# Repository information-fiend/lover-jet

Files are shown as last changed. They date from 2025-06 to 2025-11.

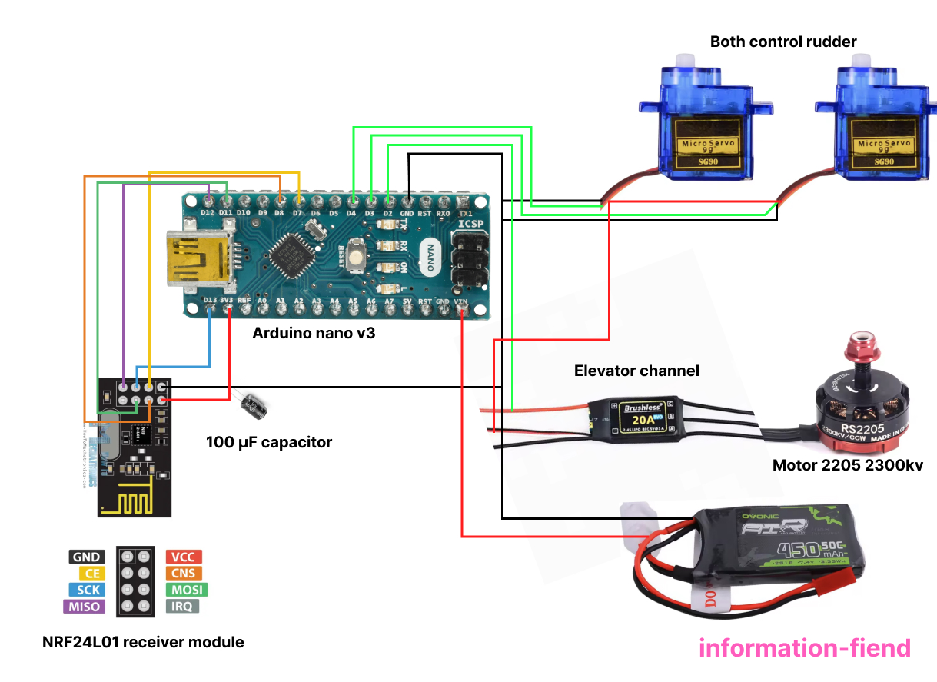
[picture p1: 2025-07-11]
Wiring diagrams/wiring diagram 3.jpg

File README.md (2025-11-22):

<h2 align="center">
 
 Lover Jet: RC F-22 Raptor
</h2>
&nbsp;

> A lover, not a fighter. :warning: Not to mock or make light of warfare

A 4-channel RC system consisting of a Arduino Nano-based transmitter and a cardboard F-22 Raptor jet powered by brushless propulsion. It uses NRF24L01+ transceivers for communication. Made this as an introduction to aerospace systems, more to come :)

### 📷 Pictures




Screenshot 2025-07-10 at 10 28 30 PM
(Cardboard jet hasnt been cut out yet)

### BOM
|Qty| Device|	Link	|Cost	|
|---|-----|---|---|
1|Cardboard 60x85cm|Me|N/A
1|Motor 2205 2300kv|[Link](https://www.aliexpress.us/item/3256806652883904.html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)|$0.99
1|Propeller 5045|[Link](https://www.aliexpress.us/item/3256806957215026.html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)|$5.53
1|ESC 20A FMS|[Link](https://www.aliexpress.us/item/3256807612408276.html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)|$0.99
2|Servo 9g|[Link](https://www.aliexpress.us/item/3256805670877496.html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)|$0.99
1|NRF24L01 receiver module|[Link](https://www.aliexpress.us/item/3256807924390952.html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)|$3.64
2|7.4v 450mah li-po battery|[Link](https://www.aliexpress.us/item/3256807759429745.html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)|$11.58
2|Arduino nano v3.0|[Link](https://www.amazon.com/LAFVIN-Board-ATmega328P-Micro-Controller-Arduino/dp/B07G99NNXL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)|$15.99
2|KY-023 joystick|[Link](https://www.aliexpress.us/item/3256807375670744.html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)|$1.77
1|NRF24L01 + PA|[Link](https://www.aliexpress.us/item/3256805495903750.html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)|$2.30
1|Single Pole Single Throw (SPST) Switch|[Link](https://www.aliexpress.us/item/3256808934087455.html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)|$1.48
1|EC11 rotary encoder|[Link](https://www.aliexpress.us/item/3256807457768762.html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)|$2.15
1|Voltage regulator 7805|[Link](https://www.aliexpress.us/item/3256807345258850.html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)|$1.95
2|100 µF capacitor|[Link](https://www.aliexpress.us/item/3256805372329013.html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)|$1.99
2|10 µF capacitor|[Link](https://www.aliexpress.us/item/3256805372329013.html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)|$1.99
1|AMS1117-3.3v|[Link](https://www.aliexpress.us/item/3256808067206574.html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)|$1.99
1|pcb| |$20.00
| | | |= $77.32

 <p align="center">
  
</p>

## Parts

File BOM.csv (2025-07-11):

Qty | Device | Link | Cost
1 | Cardboard 60x85cm | Me | N/A
1 | Motor 2205 2300kv | https://www.aliexpress.us/item/3256806652883904.html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 | $0.99
1 | Propeller 5045 | https://www.aliexpress.us/item/3256806957215026.html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 | $5.53
1 | ESC 20A FMS | https://www.aliexpress.us/item/3256807612408276.html | $0.99
2 | Servo 9g | https://www.aliexpress.us/item/3256805670877496.html | $0.99
1 | NRF24L01 receiver module | https://www.aliexpress.us/item/3256807924390952.html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 | $3.64
2 | 7.4v 450mah li-po battery | https://www.aliexpress.us/item/3256807759429745.html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 | $11.58
2 | Arduino nano v3.0 | https://www.amazon.com/LAFVIN-Board-ATmega328P-Micro-Controller-Arduino/dp/B07G99NNXL?xpid=BLck2ap9v-6h8 | $15.99
2 | KY-023 joystick | https://www.aliexpress.us/item/3256807375670744.html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 | $1.77
1 | NRF24L01 + PA | https://www.aliexpress.us/item/3256805495903750.html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 | $2.30
1 | Single Pole Single Throw (SPST) Switch | https://www.aliexpress.us/item/3256808934087455.html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 | $1.48
1 | EC11 rotary encoder | https://www.aliexpress.us/item/3256807457768762.html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 | $2.15
1 | Voltage regulator 7805 | https://www.aliexpress.us/item/3256807345258850.html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 | $1.95
2 | 100 µF capacitor | https://www.aliexpress.us/item/3256805372329013.html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 | $1.99
2 | 10 µF capacitor | https://www.aliexpress.us/item/3256805372329013.html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 | $1.99
1 | AMS1117-3.3v | https://www.aliexpress.us/item/3256808067206574.html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 | $1.99
1 | Perfboard | https://www.aliexpress.us/item/3256806952917702.html?scm_id=1007.40196.439370.0&scm-url=1007.40196.439370.0 | $1.99
1 | pcb |  | $20.00
 |  |  | $77.32

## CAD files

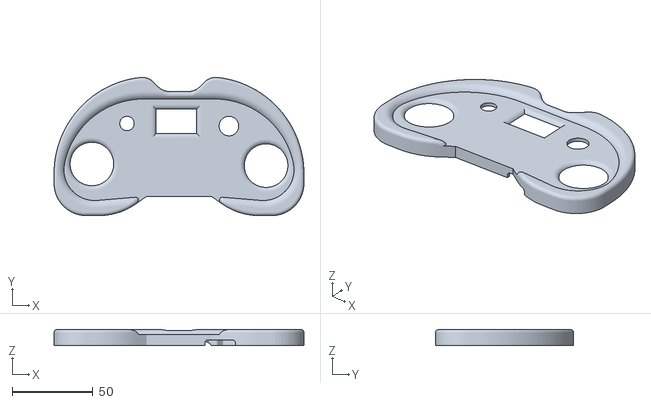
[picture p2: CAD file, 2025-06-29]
Production/front.stl
155.0 x 85.7 x 10.0

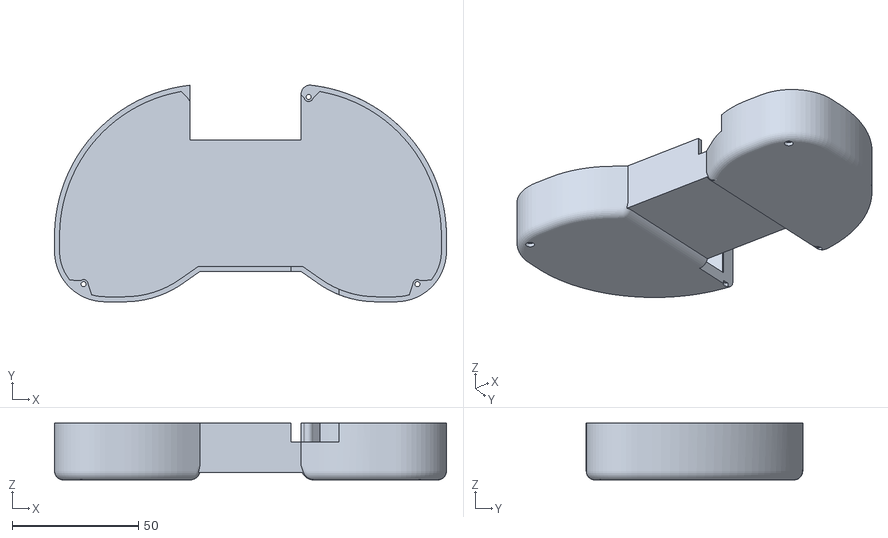
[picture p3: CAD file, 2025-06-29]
Production/back.stl
155.0 x 85.7 x 22.5

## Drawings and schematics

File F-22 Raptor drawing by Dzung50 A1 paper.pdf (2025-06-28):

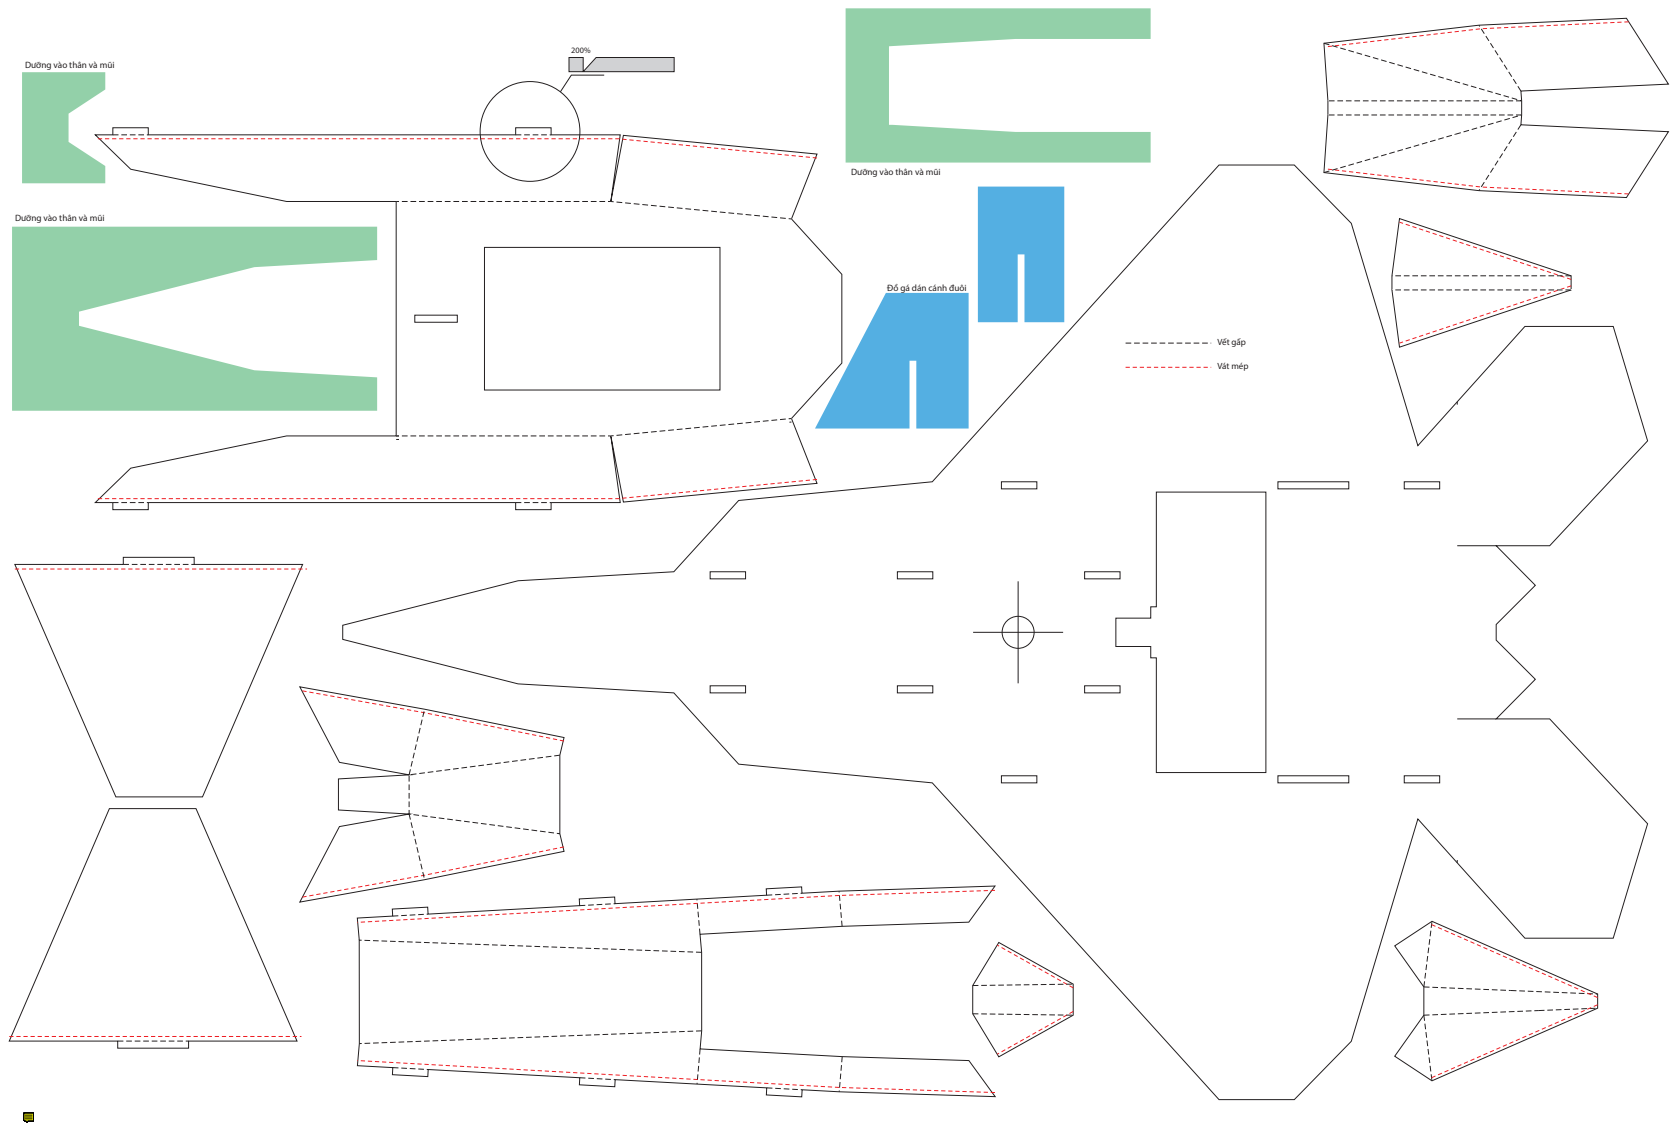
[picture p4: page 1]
Vết gấp; Vát mép

Dưỡng vào thân và mũi

Đồ gá dán cánh đuôi

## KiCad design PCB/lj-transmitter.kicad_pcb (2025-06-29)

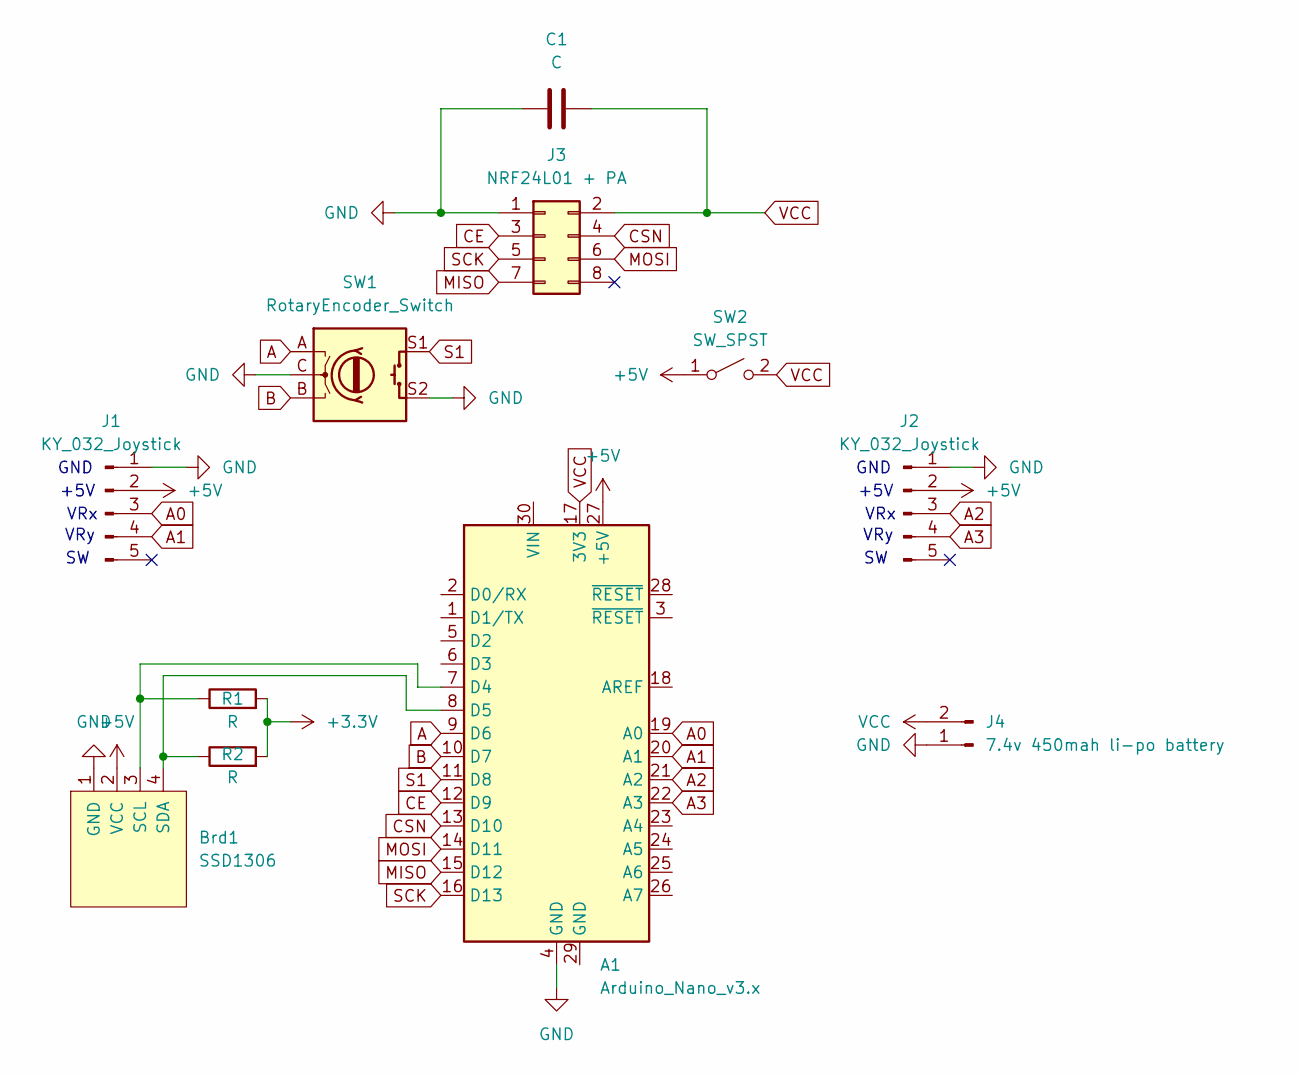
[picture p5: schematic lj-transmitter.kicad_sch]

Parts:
A1: Arduino_Nano_v3.x; Arduino_Nano
Brd1: SSD1306; 128x64OLED
C1: C; CP_Radial_D8.0mm_P5.00mm
J1, J2: KY_032_Joystick; PinHeader_1x05_P1.00mm_Vertical
J3: NRF24L01 + PA; nRF24L01_Breakout
J4: 7.4v 450mah li-po battery; BatteryHolder_Keystone_3034_1x20mm
R1, R2: R; R_Axial_DIN0207_L6.3mm_D2.5mm_P7.62mm_Horizontal
SW1: RotaryEncoder_Switch; RotaryEncoder_Alps_EC11E-Switch_Vertical_H20mm_CircularMoun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
SW2: SW_SPST; SW_CW_GPTS203211B

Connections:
+3.3V: R1.2, R2.2
+5V: A1.27 (+5V), Brd1.2 (VCC), J1.2, J2.2, SW2.1 (A)
A: A1.9 (D6), SW1.A
A0: A1.19 (A0), J1.3
A1: A1.20 (A1), J1.4
A2: A1.21 (A2), J2.3
A3: A1.22 (A3), J2.4
B: A1.10 (D7), SW1.B
CE: A1.12 (D9), J3.3
CSN: A1.13 (D10), J3.4
GND: A1.4 (GND), Brd1.1 (GND), C1.1, J1.1, J2.1, J3.1, J4.1, SW1.C, SW1.S2
MISO: A1.15 (D12), J3.7
MOSI: A1.14 (D11), J3.6
unnamed: A1.7 (D4), Brd1.3 (SCL), R1.1
unnamed: A1.8 (D5), Brd1.4 (SDA), R2.1
S1: A1.11 (D8), SW1.S1
SCK: A1.16 (D13), J3.5
VCC: A1.17 (3V3), C1.2, J3.2, J4.2, SW2.2 (B)

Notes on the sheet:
VRy
+5V
GND
VRx

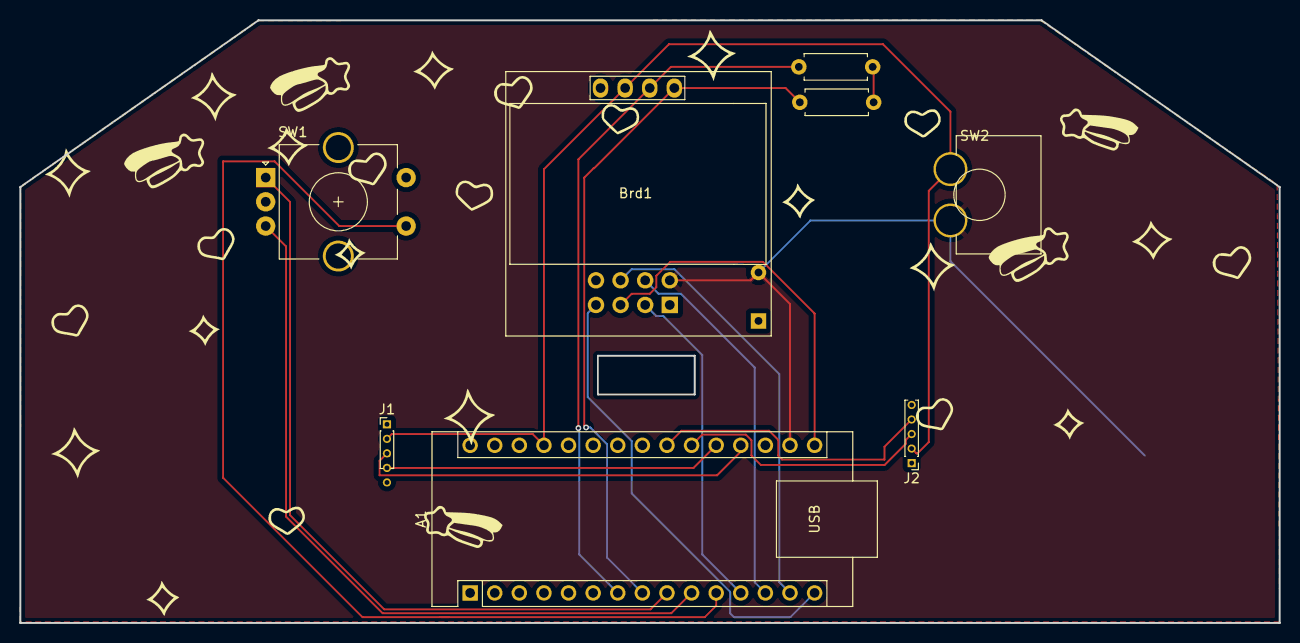
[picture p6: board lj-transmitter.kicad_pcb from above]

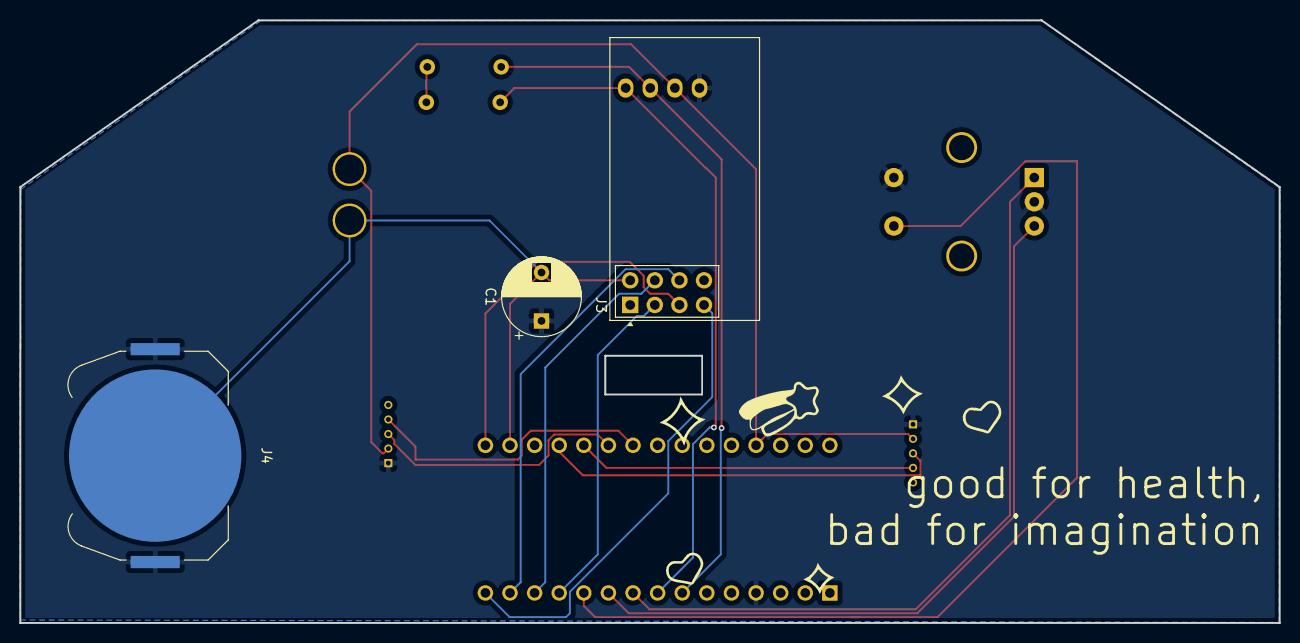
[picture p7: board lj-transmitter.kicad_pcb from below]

Board: 2 copper layers, 130.0 x 62.2 mm, 11 parts (3 on the bottom side), 18 nets.

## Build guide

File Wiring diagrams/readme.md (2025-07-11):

this is the wiring for the plane itself.
#1 is one i got from YT, shows the wires better. 
#2 i made on figma. its all the parts im using exactly.

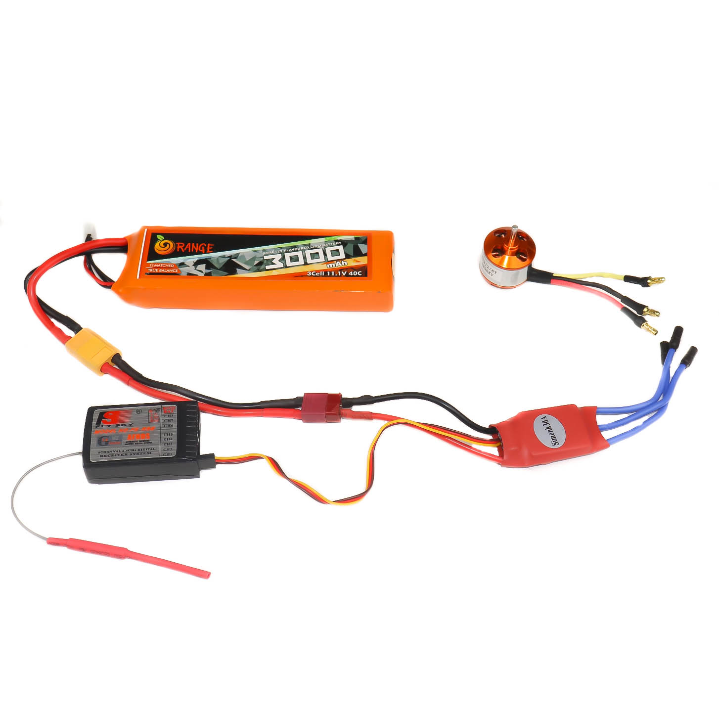
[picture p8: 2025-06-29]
Wiring diagrams/wiring diagram 1.jpg

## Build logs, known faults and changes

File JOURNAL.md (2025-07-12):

---
title: "lover-jet"
author: "info-fiend"
description: "F-22 Raptor with transmitter"
created_at: "2025-06-27"
---
### :revolving_hearts: Total Time Spent: 34hrs
June 27, 2025
---
*LOG #001:*
SPEED RUNNNNNN! rabbitboard took way too long (exactly a month). wanna get this done by the end of June cause July is busyyy. so first i started with a document and wrote everything about the project. at first it was just going to be the RC plane, but transmitters are $$$ so im gunna make that too. then i watched a bunch of vids on i. indidentally, it seems the transmitter is going to be more work than the plane 0_o. i was just going to stick a nano and antenna on a perfboard but we care about aesthetics around here. i started with making the wiring diagrams for both the transmitter and plane. started on wowki bcos i was too lazy to make a tinkercad account. am going to switch there probably. so a problem im running into is that i dont know a lick of C++, so making the firmware for the tranmitter makes me cry. <br/><br/>PLANE MATERIALS: 
* cardboard
* motor 2205 2300kv
* propeller 5045
* esc 20A FMS (eletric speed controller thing)
* 2x servos 9g
* LiPo battery
* mc6re reviever 
<br/><br/>TRANSMITTER MATS: 
* battery
* 2x joy sticks
* arduino nano
* antenna
* on/off switch
* rot encoder
* cad
* pcb

File 1
File 2
File 3
File 4

TIME SPENT: 8 HOURS

June 28, 2025
---
*LOG #002:*
start time: 4:30am. had a psychosic vision on this and got to work
okay i'm back and it's the next morning bc i fell asleep. never slept so deeply before lol. i finished around 10pm, i cut a couple hours from the time for humans needs. 
i started wrapping up the wiring diagram for the plane, then i moved to pcb making, my second worst nightmare (first is fusion360). i was still new to pcb making so it took a long time for me to realize i don't need the exact footprint, just a connector a name the pins. god bless grabcad for the 3d models. i learned the wonders of a grandpour so wiring didn't take much time. had to update my parts: 
* 7.4v 450mah li-po battery
* XY axis joystick
* Arduino nano v3.0
* NRF24L01 + PA
* Single Pole Single Throw (SPST) Switch
* EC11 rotary encoder

it's time for 3d design D:





Screenshot 2025-06-28 at 10 11 05 PM

TIME SPENT: 12 HOURS

June 29, 2025
---
*LOG #003:*
thought the cad would take longer but fusion360 decided to grace me today. the pcb was haphazardly done which was a nightmare to get things symmetrical with the case. looks good til you look at the back lol. the case is around 155x86x32.5 mm. some troubles i ran into was making it look aesthetic, as well as the screws. i was originally going to make snap joints but didnt know what the material filment was gunna be. so im using M2 screws. and if it doesnt work then hot glue!! :p
i had no idea how to make it more detailed or cuter, so i thought i'd just slap a sticker on it or paint it. i really wanna get caps for the joysticks!
by this point i also made a page in the magazine, but didnt include that time in here. 
i also want to do something to elevate this whole project but idkk. 




Screenshot 2025-06-29 at 1 25 40 PM

TIME SPENT: 6 HOURS

July 11, 2025
---
*LOG #004:*
wow where have i been? last time i finished up the case. while making up the BOM to submit, i realized i got the parts wrong on the plane + had to redesign the pcb. uhh i was first off using the wrong receiever. the battery on the transmitter had no regulator, the nrf module needs a 3.3v but it was just giving it 7.4v directly. whoops. added the same nrf receiver module so like... it matches? honestly im glad that i had to redo the design because it taught me that iterating is just a part of engineering. no avoiding it lol. uhh i made the firmware. added the libraries. prob have to make a new communication address. its kinda hard making up the firmware when you dont have the hardware </3

Screenshot 2025-07-11 at 11 05 53 AM
Screenshot 2025-07-11 at 10 35 35 AM
Screenshot 2025-07-10 at 10 28 30 PM


TIME SPENT: 8 HOURS

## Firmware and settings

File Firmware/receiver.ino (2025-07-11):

#include <SPI.h>
#include <nRF24L01.h>
#include <RF24.h>
#include <Servo.h>

// NRF24L01 communication address
const uint64_t pipeIn = 0xE8E8F0F0E1LL;

int ch_width_1 = 0;
int ch_width_2 = 0;
int ch_width_3 = 0;

Servo ch1;
Servo ch2;
Servo ch3;


struct Signal {
  byte ch1;
  byte ch2;
  byte ch3;
};

Signal data;

RF24 radio(9, 10);

void ResetData() {
  data.ch1 = 127;
  data.ch2 = 127;
  data.ch3 = 0;  
}

void setup() {
  // Attach each channel to a specific arduino pin
  ch1.attach(3);
  ch2.attach(4);
  ch3.attach(5);


  ResetData();

  radio.begin();
  radio.openReadingPipe(1, pipeIn);
  radio.setChannel(110);            // Set communication channel
  radio.setAutoAck(true);          // Disable auto acknowledgment
  radio.setDataRate(RF24_1MBPS);  // Set lowest data rate for stability
  radio.setPALevel(RF24_PA_MAX);    // Set maximum transmission power
  radio.startListening();           // Start listening for incoming data

  pinMode(2, OUTPUT);
}

unsigned long lastRecvTime = 0;

void recvData() {
  while (radio.available()) {
    radio.read(&data, sizeof(Signal)); 
    lastRecvTime = millis();          
  }
}

void loop() {
  recvData();  

  unsigned long now = millis();
  if (now - lastRecvTime > 1000) {
    ResetData();  
  }

  // Map received values to PWM pulse width range
  ch_width_1 = map(data.ch1, 0, 255, 700, 2400);
  ch_width_2 = map(data.ch2, 0, 255, 700, 2400);
  ch_width_3 = map(data.ch3, 0, 255, 1000, 2000);

  // Send PWM signals to servo motors
  ch1.writeMicroseconds(ch_width_1);
  ch2.writeMicroseconds(ch_width_2);
  ch3.writeMicroseconds(ch_width_3);
}

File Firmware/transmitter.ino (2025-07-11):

#include <SPI.h>
#include <nRF24L01.h>
#include <RF24.h>

const uint64_t pipeOut = 0xE8E8F0F0E1LL;

RF24 radio(9, 10);

struct Signal {
  byte ch1;
  byte ch2;
  byte ch3;
};

Signal data;

void ResetData() {
  data.ch1 = 127;
  data.ch2 = 127;
  data.ch3 = 0;
}

void setup() {
  radio.begin();
  radio.openWritingPipe(pipeOut); 
  radio.setChannel(110); 
  radio.setAutoAck(true);
  radio.setDataRate(RF24_1MBPS); 
  radio.setPALevel(RF24_PA_MAX); 
  radio.stopListening(); 
  ResetData(); 
}

int Border_Map(int val, int lower, int middle, int upper, bool reverse) {
  val = constrain(val, lower, upper); 
  if (val < middle)
    val = map(val, lower, middle, 0, 128); 
  else
    val = map(val, middle, upper, 128, 255); 
  return (reverse ? 255 - val : val); 
}

void loop() {
  data.ch1 = Border_Map(analogRead(A1), 0, 512, 1023, true); // CH1 (Reversed)
  data.ch2 = Border_Map(analogRead(A0), 0, 512, 1023, true); // CH2 (Reversed)
  data.ch3 = Border_Map(analogRead(A2), 560, 850, 1023, false); // CH3 (Single Side ESC)

  radio.write(&data, sizeof(Signal));
}

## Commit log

2025-06-29 Add files via upload
    diagram 1 is from YT, shows the wires a lil better
2025-06-29 added CAD
    [back.stl, front.stl]
2025-07-11 updated pcb
2025-07-11 updated wiring diagram
2025-07-11 final BOM
    [BOM.csv]
2025-07-11 add BOM
